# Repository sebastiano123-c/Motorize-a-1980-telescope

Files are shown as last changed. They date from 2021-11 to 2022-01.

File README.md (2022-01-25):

<!-- <div align="center">
<img src="https://static.tvtropes.org/pmwiki/pub/images/HHguide.jpg"  width="120" height="150">
</div>
<div align="center">"Always know where your towel is"  -   Hitchiker's guide to the galaxy </div> -->
<h1 align="center">
  <b>
    Motorize-a-1980-telescope
  </b>
</h1>
<h3  align="center" style="font-style:italic; color: Gray">Kepler1 - a OnStep project</h3>
<p align="center">
   
  
</p>
<!-- 
<h position='center'>
# Motorize-a-1980-telescope
## _Kepler1 - a OnStep project_
</h> -->

# Description
If you, like me, find an old dusty telescope in our garage, wouldn’t you want it to work like one of the best motorized telescopes? Here, you will find the transformation of my equatorial Urania telescope on the way to 2.0.

# Theory
All the steps are reported in the [documentation](https://github.com/sebastiano123-c/Motorize-a-1980-telescope/blob/main/documentation.pdf).
The software parts are provided by [OnStep](https://github.com/hjd1964/OnStep) and there you'll find how to install the software and choose your best approach that fits your mount.
3D printed parts are stored in the [Hardware](https://github.com/sebastiano123-c/Motorize-a-1980-telescope/tree/main/Hardware) folder.
Pinout design for the electronic parts are visible in the [Setup](https://github.com/sebastiano123-c/Motorize-a-1980-telescope/tree/main/Setup) folder.

# Roadmap
In the future, we will try to obtain better tracking resolutions and faster slew rates.

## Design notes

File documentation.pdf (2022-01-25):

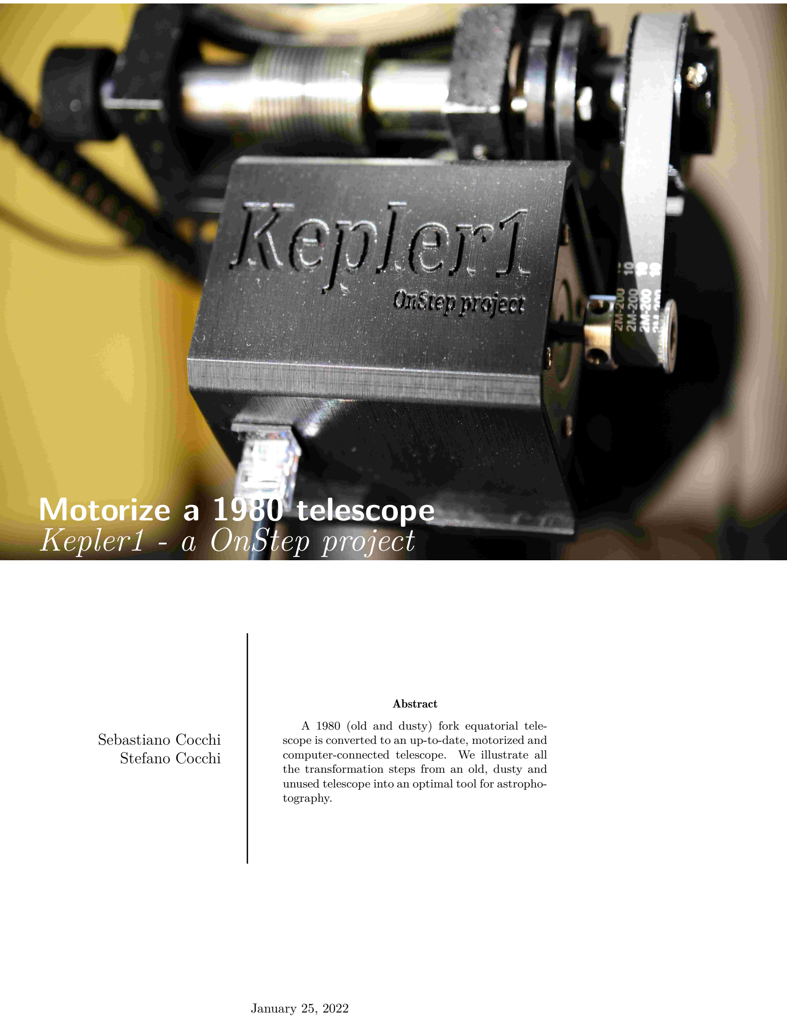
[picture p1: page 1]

# Motorize a 1980 telescope Kepler1 - a OnStep project

Sebastiano Cocchi
Stefano Cocchi

Abstract

A 1980 (old and dusty) fork equatorial telescope is converted to an up-to-date, motorized and computer-connected telescope. We illustrate all the transformation steps from an old, dusty and unused telescope into an optimal tool for astrophotography.

January 25, 2022

## Contents

Introduction | 1
1 Telescope description | 1

1.4 Telescope substitution: from Urania’s tube to

2 Electronics | 2

2.6 Sensors: WiFi connection, Real time clock

3 Mechanization | 6
4 Cable management | 6
5 The software | 8
6 Tests | 9
7 Conclusion | 9
Appendix | 11

## Introduction

The Kepler1 project led to the developing of a telescope mount with right ascension (RA), declination (DEC) and focuser (FOC) movements fully motorized and controlled by the won-
derfull software OnStep with a precision well below 1 | ′′ in both

RA and DEC mechanism starting from a 1980 telescope. The final setup components are reported in section 7, go there to find out our conclusions.
In section 1 we describe the starting telescope mount, the substitution of the old telescope tube with a new one and the installation of the latter.
In section 2 we show the electronics we have used; starting from the ESP32 board WeMos D1 R32 with CNC3 shield we describe the motor drivers, the components for the WiFi connection, the time clock and the weather sensors. We also describe some modifications to the CNC3 shield to improve the microstepping control with gotos.
In section 3 we describe the mechanisms for the RA movement, some versions of the DEC movements and the FOC motorization.
In section 4 we explain how to cleverly attach and detach the motors from the main board using ethernet cables.
In section 5 we explain the basics of the software OnStep and some additional apps that we use for the tracking (i.e. PHD2) and Stellarium.
In section 6 we briefly show the tracking system and some guiding tests operated with the mount with the results.
The result of our work is the telescope in figure 1.

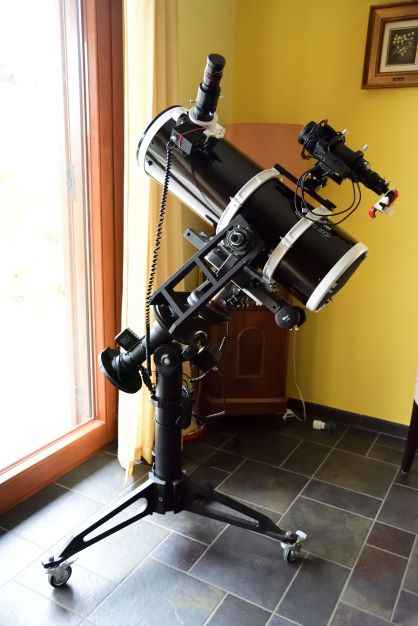
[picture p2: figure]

Figure 1: Final result: our brand-new telescope.

## 1 Telescope description

The starting point of the project is of course the telescope. In our garage, for many years, a 1980 Urania telescope has eaten a lot of dust. The telescope’s mirror resent of years in humidity and temperature jumps in the garage. In the beginning, we have cleaned the mirror with soap and water, but still seemed to be a bit compromised. We do not talk long about this telescope, since we have soon substituted it with a brand-new Skywatcher Quattro. The latter is placed on the Urania mount, since it is still a nice mount and, in our advice, has still not surpassed robustness. Indeed, the mount is a very heavy (telescope and mount totally weight 35kg!) equatorial and motorized (still works!) mount.

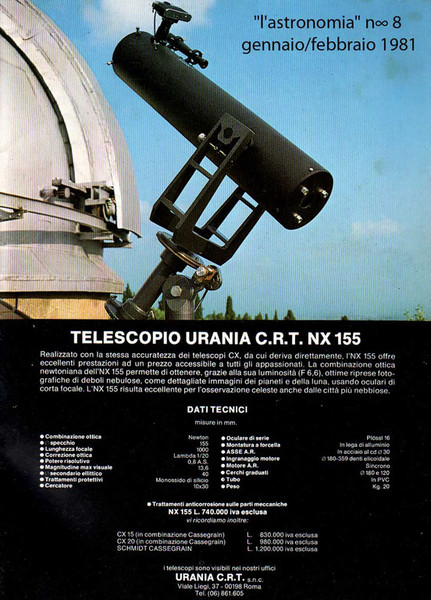
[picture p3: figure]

(a) Urania telescope and mount.

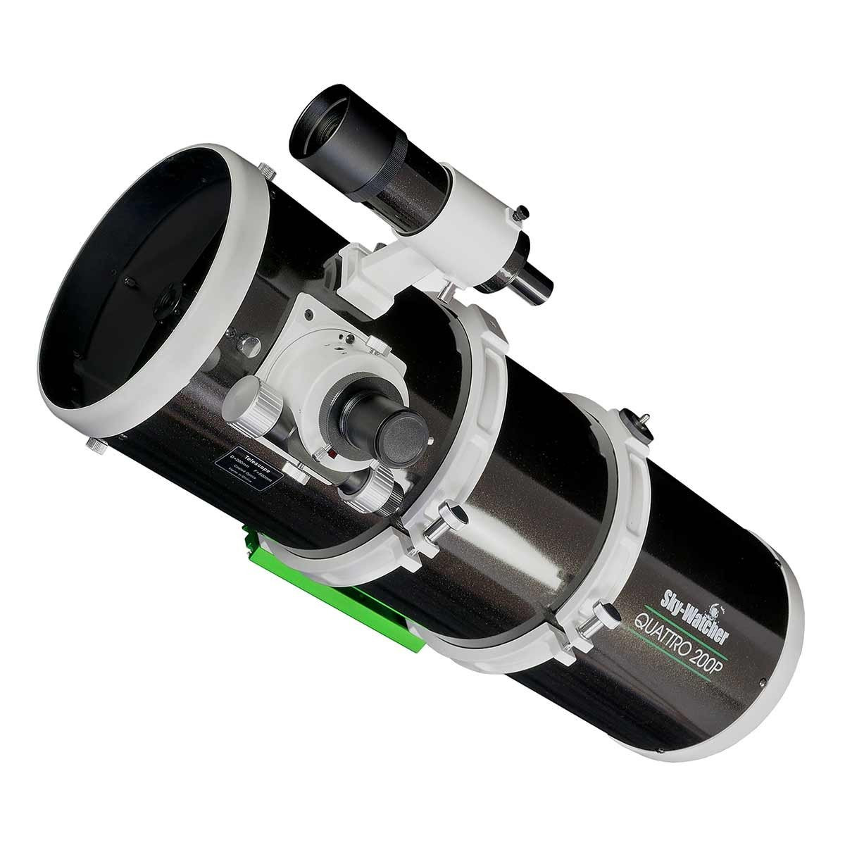
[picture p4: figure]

(b) Skywatcher Quattro telescope.

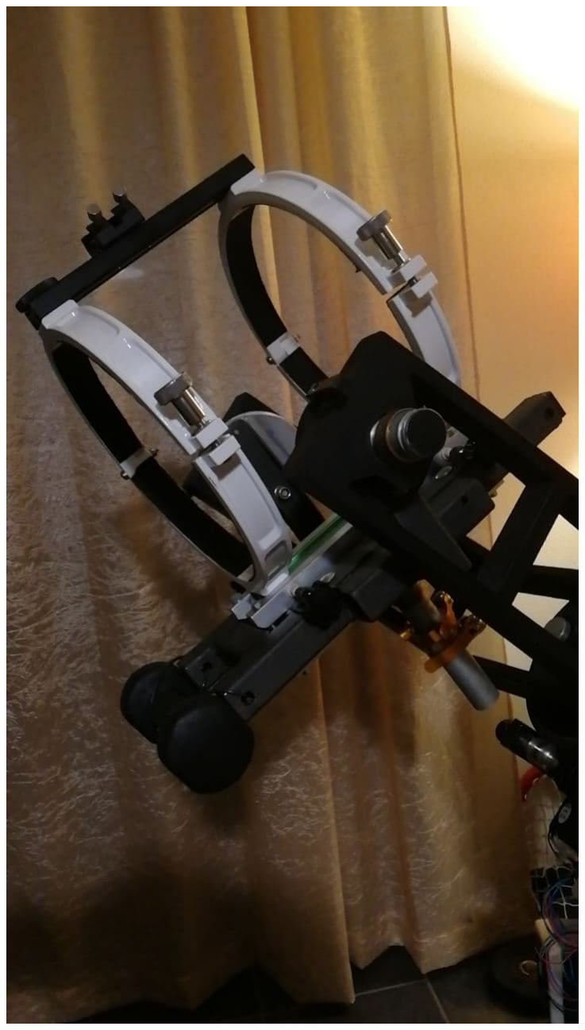
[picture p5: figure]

(c) The mechanism built to insert Skywatcher’s telescope into the Urania robust mount.

Figure 2: The transition between the old telescope to the new telescope: (a) the starting point telescope, (b) the new telescope, (c) and
(d) the telescope seat used for the substitution.

For our money, but most importantly for our fun and entertainment, we decided to modernize our old telescope.

### 1.1 Urania telescope

We briefly add the specifics of the old Urania telescope, as a sort of respect for many years of honorable work before the deep dark in the garage.
The telescope is a Urania C.R.T. NX 155, as the one in figure 2a.
Specific’s name | value
type | reflector
technique | Newton
material | PVC
weight (kg) | 10
aperture (mm) | 155
focal length (mm) | 1000
focal | f/6.5
resolution power | 0.8
limit magnitude value (mag) | 13.6
Mirror Treatment | Silica monoxide

Table 1: Urania C.R.T. NX 155 specifics.

### 1.2 Telescope’s mount

The telescope is place onto an aeronautic Aluminum tripod equatorial mount.

Specific’s name | value
weight (kg) | 25kg
type | fork
material | Aluminum alloy
RA axis diameter (mm) | 30
RA axis material | cadmium steel
RA motor | 3W synchronous

Table 2: Urania’s mount specifics.

Starting from the bottom: three pods of 45cm depart from a central post. Each one has a wheel which permits the structure to move freely and then to fix the position using stops. The central post terminates with the second axis holder whose inclination can be adjusted using a big screw. Using a digital inclinometer we fix the axis to be at 45.75′ with respect to the ground.

This axis must be aligned with the Polar star (labelling the North). In this way, a 220 volt AC 3W synchronous motor can follow the sky movement.

Departing from this second axis, a two-arms fork is free to rotate around two degrees-of-freedom defining the right ascension (RA) and the declination (DEC). The two arms are separated by the distance d = 260mm which is enough to fit the Urania telescope aperture.

### 1.3 Skywatcher 8P Quattro telescope

Skywatcher 8P Quattro Newtonian telescope (figure 2b) offers an optimal astrophotography performance. For this reason we have decided to substitute the Urania telescope with this brand-new Skywatcher telescope.

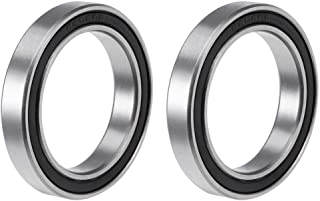
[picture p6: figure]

(a) Internal bearing mounted on one fork arm.

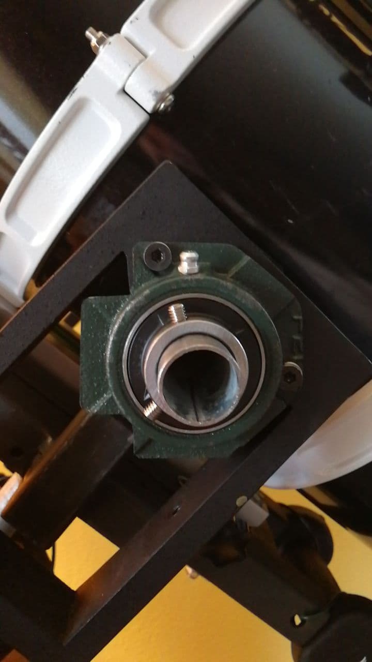
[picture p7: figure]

(b) External bearing mounted on one fork arm.

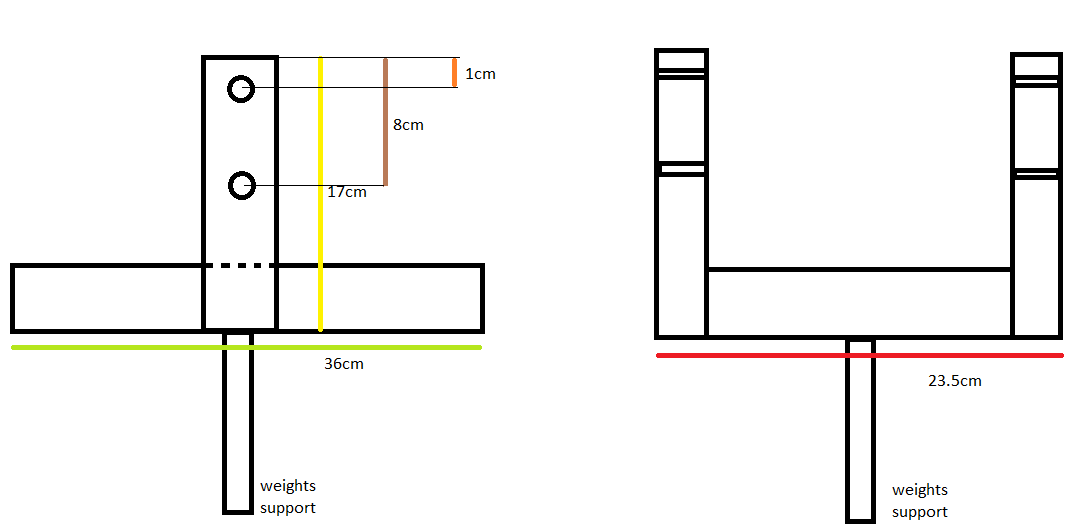
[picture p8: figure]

(c) Schematic view of the telescope mount insertion. This represents only the installation build with some squared metal bars upon which the two white loops (which hold the telescope tube) are fixed and are not illustrated in this scheme. The two holes in each arm serve to fix the structure on the mount.

Figure 3: Telescope seat details.

Specific’s name | value
type | reflector
technique | Newton
material | Carbon
weight (kg) | 8.0
aperture (mm) | 200
focal length (mm) | 800
focal | f/4
resolution power | 0.58
limit magnitude (mag) | 13.3
collect light | 820
magnification | 400
Mirror Treatment | Aluminum Coating
Focuser | Crayford dual-speed 50.8/31.8

Table 3: Skywatcher 8P Quattro
Since the Skywatcher telescope does not fit in the fork, we have thought to build a "saddle" onto which placing the telescope. The specifics of this installation are shown in the following section.

### 1.4 Telescope substitution: from Urania’s tube to

Skywatcher’s tube

Passing from the Urania telescope to Skywatcher telescope we have faced the problem of how to insert the latter in the telescope mount. Indeed, since Skywatcher’s telescope tube outer diameter is 235mm it does not fit nicely inside the mount fork.

Our solution is to insert a seat in which to place the telescope, see figure 2c. The barycenter of the telescope is not centered with the DEC axis, thus we have settled a post capable of holding weights to balance the forces, see figure 3c.

The scheme with distances is visible in figure 3c.

Lastly, to enhance the fluidity of motion and reduce the backlash, the rotation mechanism is enriched with a system of two bearings for each fork arm, one is place inside, see figure 3a, and one is fixed externally on the mount, see figure 3b.

The total weight of the mount with this modification is attested on 40kg.

## 2 Electronics

The circuit design is represented in figure 4c. In this section we expose the electronic components used in the circuit.

### 2.1 ESP32

ESP32 is a series of low-cost, low-power system on a chip microcontroller with integrated Wi-Fi and dual-mode Bluetooth. We’ve bought the ESP32 D1 R32, the one in figure 4a, for better attaching the motor using the CNC shield V3 (which is briefly explained in the following).
We decided to follow the "WeMos R32 and CNC V3" On-Step project (at https://onstep.groups.io/g/main/wiki/19670). (https://onstep.groups.io/g/main/wiki/19670) OnStep is an open source software providing the control of four stepper motors (RA, DEC, focuser and rotator for astrophotography), weather sensor handling, Wi-Fi and Bluetooth connection, polar alignment and other nice features.

### 2.2 CNC Shield V3

To better optimize space and wires connections, we have bought a CNC Shield V3 (a.k.a. CNC3), see figure 4b.
It is a printed circuit board (PCB) built for 3D printers. The shield is attached directly above the ESP32. It has four slots, each one can host a motor driver, thus using this shield there can be handled four stepper motors: RA and DEC motors, first focuser and photography rotator or second focuser. This shield can be "manipulated" to obtain better performances.

### 2.3 Motor drivers

A stepper motors works only with a driver chip that controls the motor movements. Three types of drivers have been used during the configuration of the setup.

1. DRV8825;
2. TMC2209;
3. TMC2208.

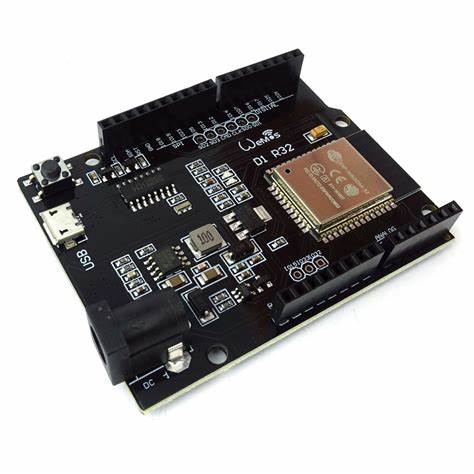
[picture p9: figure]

(a) ESP32 D1 R32 picture.

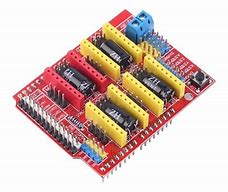
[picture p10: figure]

(b) CNC3 Shield V3.

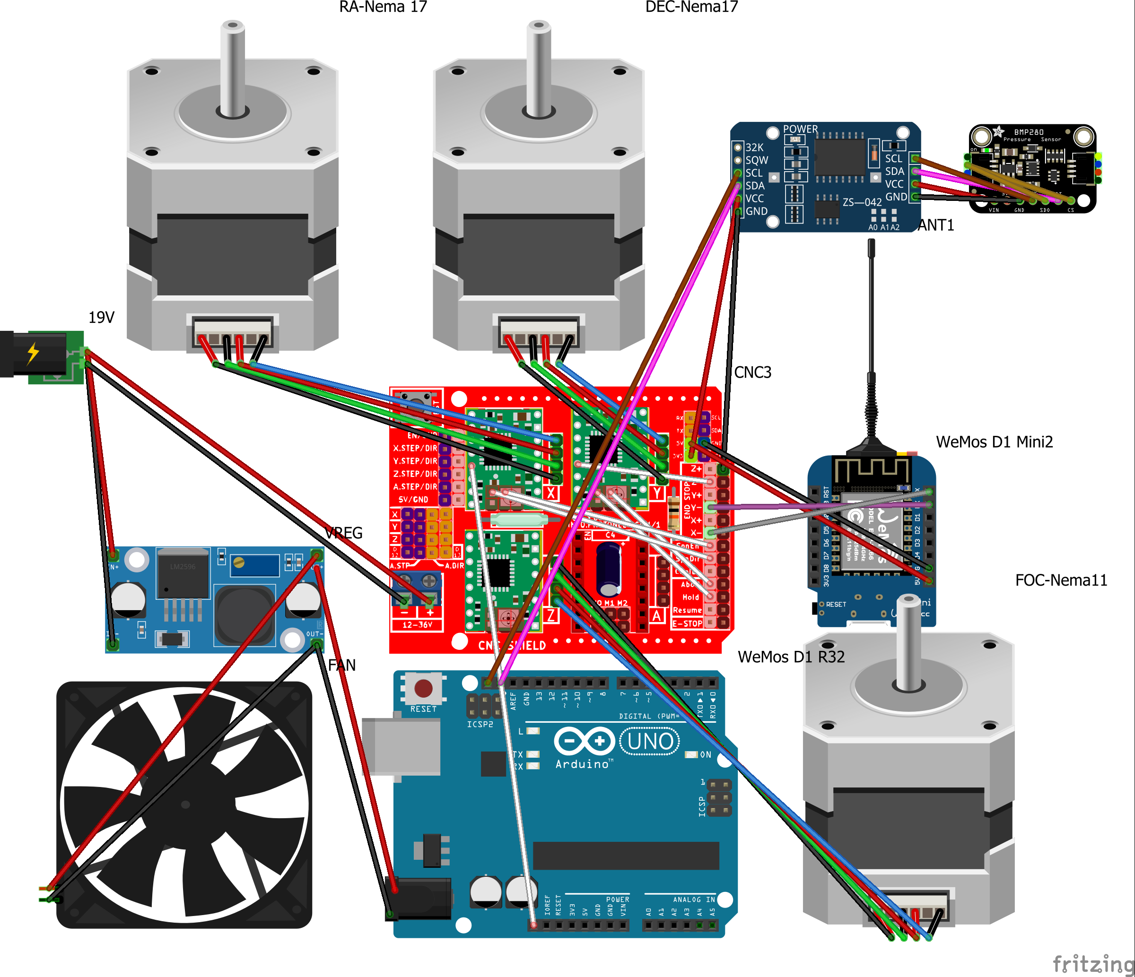
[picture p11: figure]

(c) Circuit design. Here (https://github.com/sebastiano123-c/Motorize-a-1980-telescope/blob/main/Setup/circuit-design_bb.png) can be found the png file. Figure 4: Main board components: (a) WeMos D1 R32 ESP32 board, (b) CNC shield V3 and (c) the circuit design: the Arduino board is instead a ESP32 board, like the one of figure (a); the white cables are our modifications on the board.

In each driver the right amount of current is set, otherwise the stepper motor could work improperly. This current
depends on the stepper motor current per phase parameter. Typically, drivers have a tunable screw for the tension Vref . For each type of driver, the formula to calculate the tension Vref depending on the current/phase are different.¹
The procedure is the following:
- rotate the screw in the counter clock direction;
- using a multimeter, check that the tension is zero;
- slightly rotate the screw until the tension is the desired one.

We recommend reducing the theoretical value by a 10%-30% to prevent motor dangers.

### 2.3.1 DRV8825

For these drivers the tension to be set is roughly the half of the value of the nominal current/phase of the motor. For example, if the motor has a current/phase 1A, the tension would be 0.5V.

Current phaser (A) | Current (A)
0.90 | 0.45
2.00 | 0.90

Table 4: DRV8828 drivers setup current. Note that we have set a value smaller than the one calculated to prevent motor to break.

### 2.3.2 TMC2208 and TMC2209

For these drivers the tension value is roughly the same of the current/phase value, e.g. if I = 1A the tension would be Vref = 1V. Be aware that the TMC2208 has a maximum current output of 1.2A.
The calculation is

I
√
2

=

325mV
110mΩ + 20mΩ

·

1
√
2

·

Vref
2.5V

⇒ Vref = I · 1Ω.

Remember to reduce to value by a 10%-30%.
Driver | Current/phase (A) | Current (A)
TMC2209 | 0.90 | 0.81
TMC2209 | 2.00 | 1.63
TMC2208 (focuser) | 0.67 | 0.50

Table 5: TMC22XX drivers setup current. Note that we have set a value smaller than the one calculated to prevent motor to break.

### 2.4 CNC3 and TMC2209 modifications

CNC3 shield does non permit "on the fly" change of microstepping since microsteps are achieved via the MS0/MS1/MS2 fixed jumpers below the motor drivers. This means that you cannot have different microstepping for tracking and slewing unless you use TMC2130 or TMC5160 through SPI interface. To overcome this CNC3 limit when using other drivers (e.g. TMC2209 that are very silent, guarantee a 2A current per phase and are somehow cheap), it is necessary to do some soldering on the CNC3 and on the TMC2209 and modify the pinmap "Pins.CNC3.h".

1See this (https://all3dp.com/2/vref-calculator-tmc2209-tmc2208-a4988/) for more details.

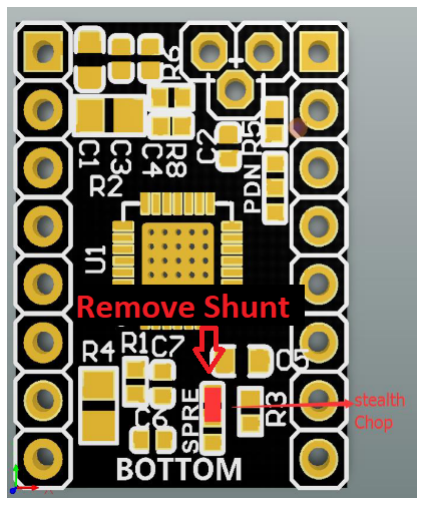
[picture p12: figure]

(a) TMC2209 driver with highlighted modifications.

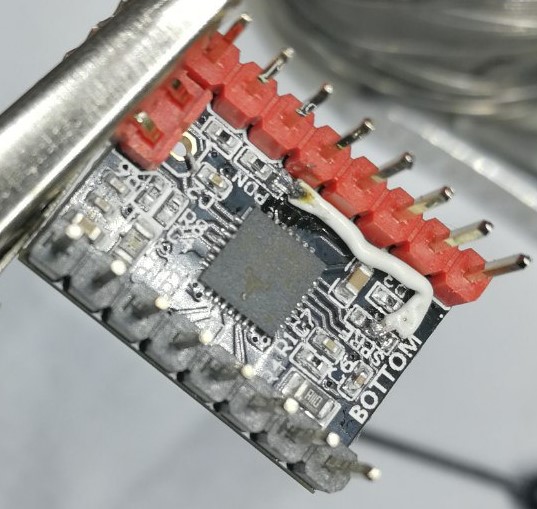
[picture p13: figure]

(b) Connection of the Spread pin to pin 5 by

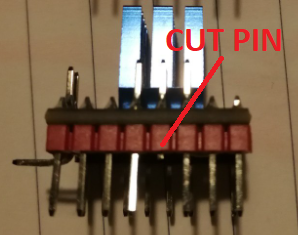
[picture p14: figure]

wire. | (c) Cut low pin 5.

Figure 5: TMC2209 modifications.

### 2.4.1 Microsteps control

First of all it is necessary to configure the TM2209 stepper driver (TMC2209 Bigtreetech v1.2) to remove the Spread shunt (that controls StealthChop vs SpreadCycle mode) on the TMC2209 board and then wire connect the Spread to pin 5 of J1, see figures 5a 5b.
Finally, you have to cut the low pin 5 of J1 on the TMC2209 driver since it is shortcutted with pin 6 (CLK) on the CNC3, see figure 5c.
At this point, we have a wire connected (some soldering) the MS0 and MS1 of Axis X to the SpnEn and SpnDir pins of CNC3 respectively. In the same way, we have a wire that connected the MS0 and MS1 of Axis Y to the HOLD and ABORT pins respectively. In this way, we are able, after modifying the pinmap in "Pins.CNC3.h" to control the microstepping in Tracking and Goto both in RA and DEC. You can find the modified Pinmap "Pins.CNC3.h" here. (https://github.com/sebastiano123-c/Motorize-a-1980-telescope/blob/main/OnStep/src/pinmaps/Pins.CNC3.h)
The last modification is simply to connect with a wire jumper pin 5 of TMC2209 of AXIS X to the pin IO0 of the We-Mos D1 R32 as well as connect pin 5 of TMC2209 of AXIS Y to the pin Z− of the CNC3. With this done we able to set programmatically (via Config.h) the SpreadCycle (StealthChop) mode using the TMC2209_QUIET (TMC2209_VQUIET) constants.
Here (https://github.com/sebastiano123-c/Motorize-a-1980-telescope/blob/main/OnStep/Config.h) is the updated "Config.h".

### 2.5 Power supply

The power supply is provided by a 19V 5A power supply as in table 6.
voltage output (V) | current output (A)
19.3 | 4.74

Table 6: Nominal tension and current outputs of the
power supply.
For our initial purposes it was enough, indeed 5A are enough to feed quite well two stepper motors and a poor electronics. A rough estimation poses 1.8A for RA motor, 0.9A for DEC motor and few milliampéres for the ESP32. The reader is strongly encouraged to check the total current its circuit needs before buying a power supply.
To provide the 3.3V tension to the microcontroller, a IC-QUANZX voltage regulator is place between the power supply and the ESP32.

### 2.6 Sensors: WiFi connection, Real time clock

(RTC) and weather sensor (BMP280)

OnStep contains the so-called Smart Web Server (SWS) that provides WiFi (or Ethernet) connections using an IP but it does not exploit the native ESP32 chip for the WiFi connection; To command the mount via WiFi a ESP8266-12F WeMos D1 mini must be connected to the CNC3.² Many devices support this type of connection including cell-phones, tablets, laptop/desktop computers, etc. Using this library, it is possible to use programs such as Stellarium via ASCOM drivers provided by the OnStep project. (http://www.stellarjourney.com/index.php?r=site/software_telescope) We have added an external antenna to enhance the WiFi connection range.³ The weather sensor BMP280 is modified as follows: the CSB and the SDO pins are connected directly to the Vcc. The sensor is then attached directly to the RTC module Ds3231. The RTC, BMP280, the WiFi module and the stepper motors are connected to the WeMos ESP32 D1 R32+CNC3 board as in figure 4c.

## 3 Mechanization

The motorization of the telescope passes through two mechanics adjustments:

1. motorize the RA movement, exploiting the native tracker mechanism;
2. motorize the DEC movement, which natively has no gears.

Before entering in the details, we define the stepper motors used in the setup.

2For the pinout maps look at this connection diagram. (https://onstep.groups.io/g/main/wiki/19670) 3Take a look at this (https://www.instructables.com/External-Antenna-for-ESP8266/) to see how to do that.

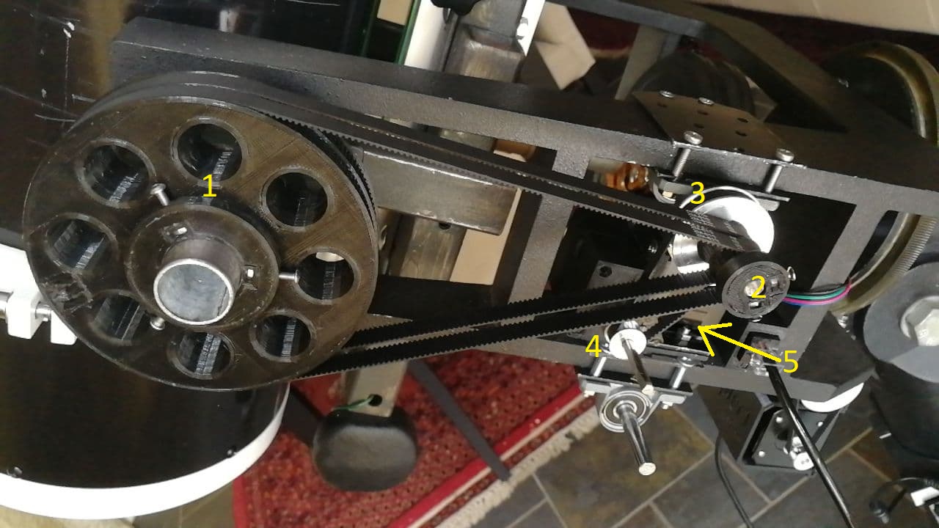
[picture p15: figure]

(a) DEC V1 mechanism.

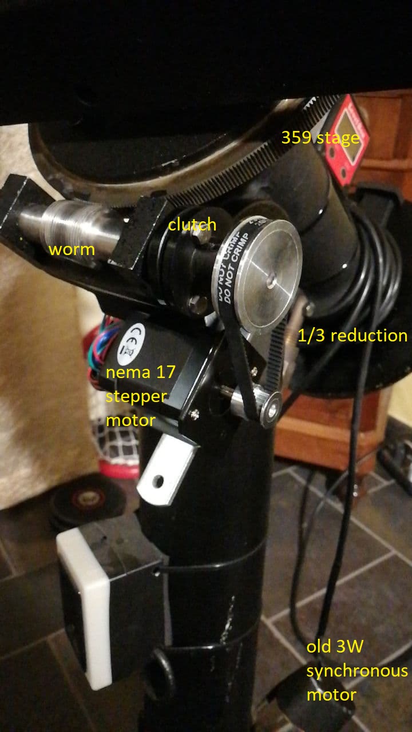
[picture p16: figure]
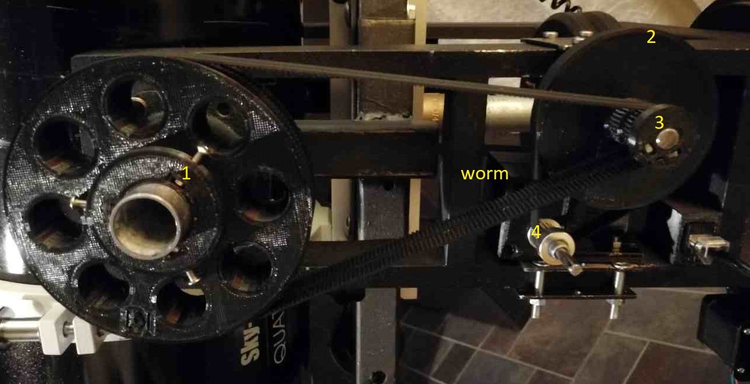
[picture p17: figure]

(a) DEC V1+ mechanism. | (b) RA mechanism.

Figure 6: RA and two of the many versions of the DEC mechanization.

### 3.1 Stepper motors

In this subsection we write the specifics of the stepper motors used for the RA and DEC mechanization (for both we have used nema 17 motors) and the focuser (developed with a nema 11 stepper motor).

### 3.2 RA motorization

The telescope’s mount has already a tracking mechanism motorized by a 220volt AC 3W synchronous motor. So, in principle, it is only a matter of substitute this old motor, with a new programmable stepper motor.
The gears are composed by:
- a 359 teeth stage (1 tooth for each degree, fantastic);
- an endless screw (worm) mounted on a shaft through a clutch.

Using this structure, for a continuous sky tracking, the elder motor would complete a round of the worm in 4 minutes. Thus, this mechanism rotates the mount with the velocity of a degree in 4 minutes (which is the velocity of the sky moving away in the night).
We have reduced the ratio by a third adding two other pulleys (see figure 6b): 60 teeth pulley positioned in the shaft and a 20 teeth pulley on the motor shaft.
ratio gear 1 | ratio gear 2 | total ratio
1/360 | 1/3 | 1/1080

Table 7: Total reduction of RA mechanization.
We have chosen to install a nema 17 stepper motor with the specifics in table 15

### 3.3 DEC motorization

The mechanization of the DEC axis was a bit more complicated since there was not a built-in gear to use. We tried different versions. A first successfully try was to exploit a stand-alone disk. On the edge of the latter are present some ticks and grades: it was used a declination angle teller.
As told above, we have tried different configurations, but same stepper motor is used.

### 3.3.1 DEC V1

Using a 3D printer we have designed a double-belt pulley. Then, a 1/10 ratio is obtained using a worm gear and another 1/3 is obtained between the worm and the final gear. The total reduction with all gear specifics is reported in table
8. Figure 6a is a picture of the mechanism. The precision of the mechanism is

δth. = 0.28′′, δest. = 0.96′′

where th. stands for theoretical and est. stands for estimated.

DEC-V1 stages
Gear number | 1 | 2 | 3 | 4 | worm
number of teeth | 180 | 30 | 60 | 20 | 10
total ratio | ∼
| 1
| 180

Table 8: DEC mechanism’s gear specifics.

### 3.3.2 DEC V1+

Starting from the DEC V1, we have designed a new gear to get a bigger reduction ratio (this is the reason for the +). The total reduction with all gear specifics is reported in table 9. Figure 6a is a picture of the mechanism. The precision of the

mechanism is

δth. = 0.14′′, δest. = 0.48′′

where th. stands for theoretical and est. stands for estimated.

DEC-V1+ stages
Gear number | 1 | 2 | 3 | 4 | worm
number of teeth | 180 | 30 | 120 | 20 | 10
total ratio | ∼
| 1
| 360

Table 9: DEC mechanism’s gear specifics.

### 3.4 Focuser motorization

Another improvement is the motorization of the dual speed Crayford focuser. Using a nema 11 stepper motor, we have created the motor supports and the gears using a 3D printer. The reduction stage is 1/3, and the mechanism is visible in figure 7c.

## 4 Cable management

The wiring between the electronics and the motors is made focusing on the main idea to attach and detach them rapidly. We thought to use Ethernet cables. They are a versatile solution but how to connect them to the four cables governing the stepper motor?
Stepper motors have four cables, see figure 8, which have to be driven to the CNC3.

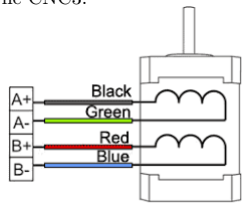
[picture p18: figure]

Figure 8: Stepper motor cables scheme.

### 4.1 Ethernet cables

Ethernet cables are composed typically by 8 thin cables, each one carrying low current, approximately 0.3 − 0.5A. Since stepper motors require currents of the order of 1A, we decided to use them in couple, according to the general Ethernet cabling scheme. Thus, the four motor cables are doubled and fixed into the eight way Ethernet socket.
Then, the main box is prepared to receive the Ethernet cables. In the most remote drawers of the garage, we have found an old and burned electronic card with four Ethernet sockets, a power supply entry and an on/off switch. Using a multimeter we have checked the pins of each slot and created the connections to the CNC3 shield.
In figures 7a, 7b and 7c are shown some examples of Ethernet wiring.

### 4.2 Plastic boxes

Using a 3D printer, we have created the focuser motor bracket with the Ethernet exit, and so we did for the RA motor. The microcontroller, the CNC3 shield, the power supply and all the electronics have been thrown in a box. The stepper motors drivers do not get hot, nevertheless we have decided to put a 12V fan in the box. In figures 7a, 7b and 7c are shown the resulting plastic boxes.

## 5 The software

Now comes the software part. In our mind, we wouldn’t want to spend much time on programming. We desired a plug-andplay solution, or something similar. A software with easily controlling and possibly which can talk via ASCOM drivers with Stellarium (or others), PHD2 and others astrophotography programs.

### 5.1 OnStep

On the internet, we have found a great, open-source, free and customizable software called OnStep.⁴ We have followed the instructions for the WeMos D1 + CNC V3 project, configured the Config.h file and upload the sketch on the ESP32 board. Finally, the box is placed on the mount and connected with the Ethernet cables to the motors. OnStep is actually a wonderfull project. Don’t miss it, and stay tuned on it!

### 5.2 PHD2

Push It Dummy-2 (PHD2) is the software that controller the auto-guiding system. PHD2 is telescope guiding software that simplifies the process of tracking a guide star, letting you concentrate on other aspects of deep-sky imaging. There are plenty tutorials on the internet showing how to use PHD2, so we do not enter so much into details.⁵ But we only want to stress out that, after few important configuration passes, the auto-guiding is really simple and promises very good results!

### 5.2.1 Wizard configuration

Connection is really simple using the "wizard" option suggested in every tutorials. The "unbinned pixel size" is one of the first parameters you have to fix in the wizard which are not quite clear. You should be able to get the unbinned pixel size from the camera spec sheet or the manufacturer’s web site. If this is not the case, you can get the unbinned pixel size by taking the dimension of the sensor and diving it by the number of pixels.
The "bin level" is the technique to combine proximal bins to form a "superpixel".⁶ This has the effect of reducing the noise but at the price of reducing the image definition. Another remarkable option to fill is the telescope mount’s driver, which in this case are the ASCOM OnStep telescope drivers.

4Wiki groups:https://onstep.groups.io/g/main/wiki/3860.
Github:https://github.com/hjd1964/OnStep.
5https://www.youtube.com/watch?v=Kd4qzW7uV38 or the pdf https://openphdguiding.org/man-dev/Basic_use.htm.6https://www.photometrics.com/learn/imaging-topics/binning-2.

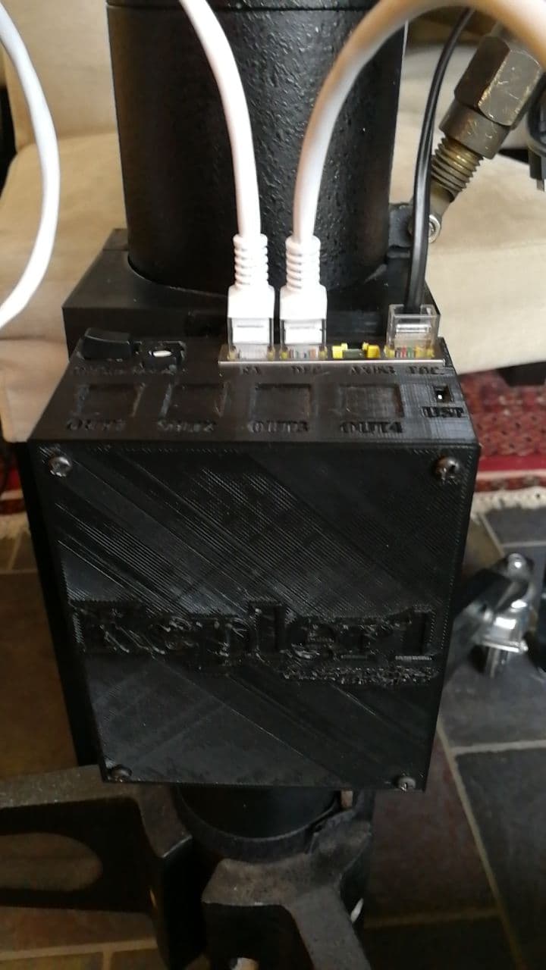
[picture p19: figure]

(a) The main box containing the electronics and its easy management Ethernet connections.

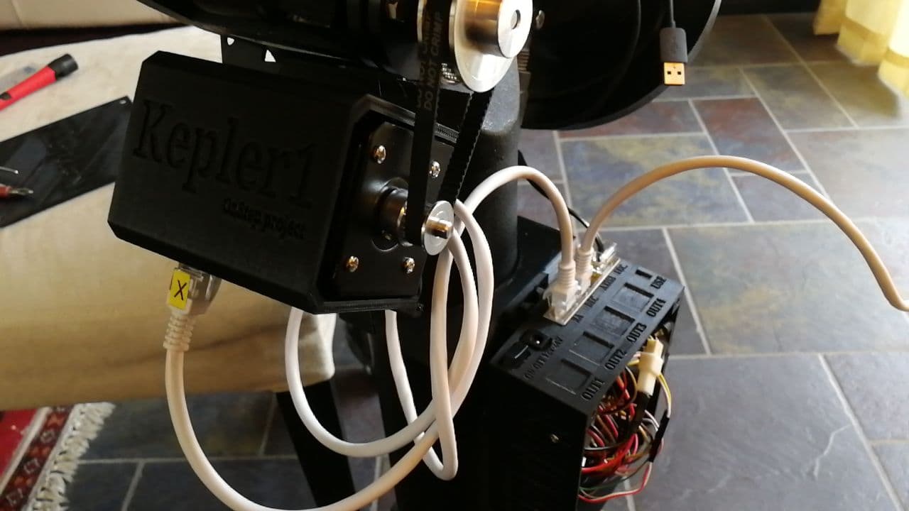
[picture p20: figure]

(b) The RA motor box containing the stepper motor and its Ethernet socket.

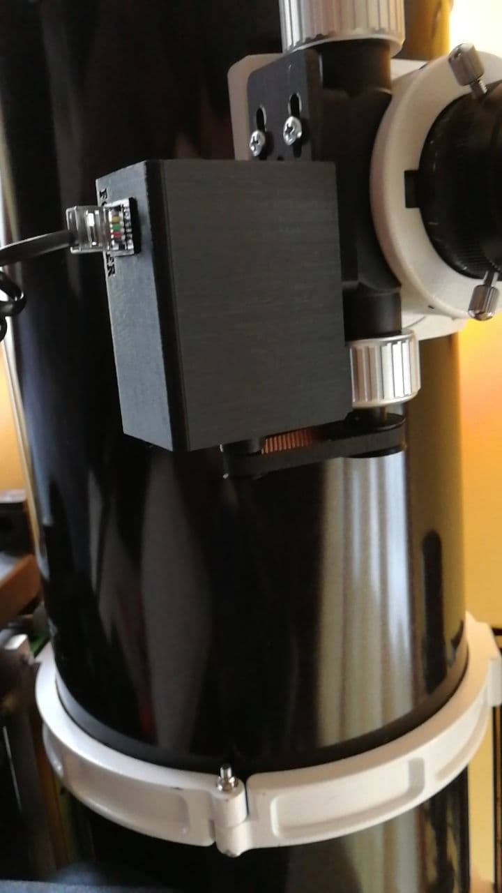
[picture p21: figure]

(c) The focuser box containing the focuser stepper motor and its Ethernet socket.

Figure 7: Plastic boxes.

### 5.2.2 Dark libraries

Before starting the first guiding session, it is useful to spend 5 minutes to create a dark library. To do so, just press the "Dark" tool on the top and create a new dark library. Cover the guidescope, and start the acquisition.
After the acquisition, remove the cover; this should make clearer acquisitions.

### 5.2.3 Connect all!

After the configuration, press the first icon in the bottom left and press "connect all". Now the camera and the mount are connected to PHD2.

### 5.2.4 Calibration

Search a bright star whose declination is between 10 to -10 degrees. Start the acquisition pressing the "cycle" icon (the second from the left), then press the "star with a magnifying glass" that selects the most bright star. Finally, push the PHD2 icon; this will start the calibration and requires few minutes.

### 5.2.5 Guiding

If dark libraries and calibration are done, the guiding can start. If it is not present, search in the settings the plot visualization that let you know the adjustments that PHD2 is doing. In our case, it is a useful tool to see if our work were precisely enough.
A useful tool is the "use multiple stars" in the guiding settings. The latter permits holding multiple star, and we think this is another improvement to stability in auto-guiding.

### 5.3 Stellarium

Stellarium is the software we use to search objects. The impressive feature is that, after paring it via ASCOM drivers with the mount, it is possible to tell the telescope to move at the star pointed out in Stellarium.⁷
The telescope is now free to start few tests to check the goodness of our work!

## 6 Tests

The test are aimed to estimate the precision of the mount. Of particular interest are the test using PHD2 which measure the precision in micro-adjustments for the auto-guiding system. The application used to study the PHD2 plots is the PHD2LogViewer app. The latter can upload all the guiding session you make, since every session is stored in the PHD2 folder. The app also make raw statistical analysis which are good parameters to think about. The root-meansquare (RMS) describe the spread of the data points around some average peak value (like standard deviation). The value of RMS should be 1 arcsecond or lower for a good guiding. Before describing the tests, let us show the tracking system, which is composed of a guidescope and a tracking camera.

### 6.1 Telescope guidescope

On the telescope is fixed a 240mm focal length guidescope Svbony SV106.

### 6.2 Guidescope camera

The camera is an old red SJ1000 action-cam inserted into the guidescope using an adapter.⁸ The result is pretty weird, but it works! Just look at the following sections PHD2 logs!

7See https://www.youtube.com/watch?v=DUdYv311HFw.
8See this useful tutorial https://telescopeguides.com/how-to-use-a-webcam-with-a-telescope/.

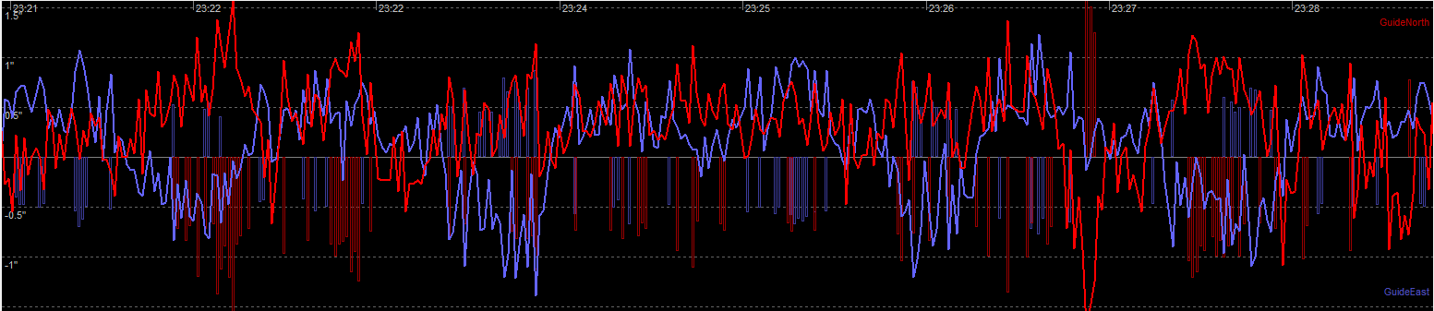
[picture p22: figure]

Figure 9: DEC V1 test: PHD2 log view using arcseconds as units. In pixel the scale is in the range [−0.4,0.4]. The sky seeing was 0.98′′

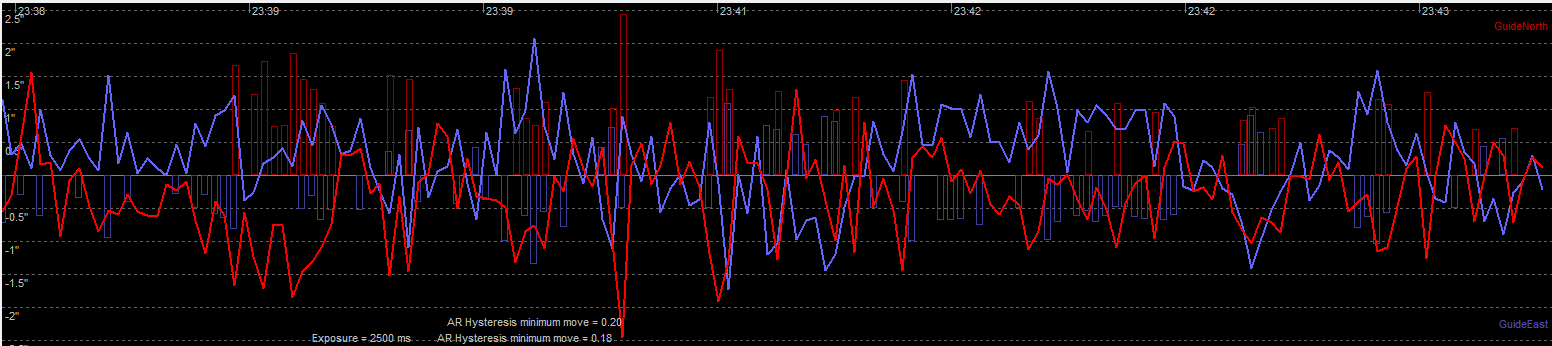
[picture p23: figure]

Figure 10: DEC V1+ test: PHD2 log view using arcseconds as units. In pixel the scale is in the range [−0.5,0.75]. The sky seeing was 1.80′′

### 6.3 DEC V1 test

The DEC V1 has been developed to reduce the mechanism backlash using the idea the less the number of belts gets, the better the guiding is. The resolution power of the mount is reported in table 10. The extrapolated statistics is reported in table 11.

Mechanism | microsteps (x360◦
) | estimated resolution (”)
RA | 19200 | 0.21
DEC | 12800 | 0.65

Table 10: Resolution power using the DEC V1 mechanism. Microsteps is intended as the total number of microsteps around the entire circumference.
After the calibration, we have pointed the Rosetta nebula and start tracking. The result can be seen in figure 9. The sky condition was very nice that night with a seeing of 0.98′′
Statistics | RMS | Peak
RA | 0.47" (0.15 px) | 1.87" ( 0.58 px)
DEC | 0.90" (0.28 px) | -8.12" (-2.52 px)
Total | 1.02" (0.32 px)
Drift | ("/min) | (px/min)
RA | +3.01"/min | +0.94 px/min
Dec | +2.14"/min | +0.66 px/min
Polar Alignment Error | 8.7’

Table 11: DEC V1 test: statistics of the guiding of figure 9.

### 6.4 DEC V1+ test

We have updated the DEC V1 mechanism to DEC V1+ to introduce a more gear reduction and the possibility to decouple the telescope movement from the gear to perfectly balance it. The resolution power of the mount is reported in table 12. The extrapolated statistics is reported in table 13.
Mechanism | microsteps (x360◦
) | estimated resolution (”)
RA | 51058 | 0.24
DEC | 25600 | 0.48

Table 12: Resolution power using the DEC V1+ mechanism. Microsteps is intended as the total number of microsteps around the entire circumference.
After the calibration, we have pointed Aldebaran and start tracking. The result can be seen in figure ??. We point out that the sky condition was not optimal since the seeing was 1.80′′. The latter parameter effect with spurious drifts the guiding.
Statistics | RMS | Peak
RA | 0.66" (0.20 px) | -2.04" (-0.63 px)
DEC | 0.63" (0.20 px) | -2.40" (-0.75 px)
Total | 0.91" (0.28 px)
Drift | ("/min) | (px/min)
RA | +3.39"/min | +1.05 px/min
Dec | -3.65"/min | -1.13 px/min
Polar Alignment Error | 14.5’

Table 13: DEC V1+ test: statistics of the guiding.

## 7 Conclusion

After lots of hours testing our telescope, we can declare what is the best configuration found using the WeMos D1 + CNC3 shield.

Part | component
Microcontroller | WeMos D1 R32 (ESP32) (https://www.amazon.it/ARCELI-sviluppo-dual-mode-Bluetooth-Arduino/dp/B07MBZMYCX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)
Pinmap | CNC3 (https://www.amazon.it/AZDelivery-CNC-Shield-V3-Development/dp/B07YWQJCNY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)
Voltage regulator | 5V (https://www.amazon.it/ICQUANZX-regolatore-Step-Down-Convertitore-Tensione/dp/B07VQ89RZG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)
Time | RTC DS3231 (https://www.amazon.it/ARCELI-DS3231-AT24C32-Precision-Arduino/dp/B07CQW5RMQ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)
Weather sensor | BMP280 (https://www.amazon.it/ARCELI-GY-BMP280-3-3-pressione-atmosferica-precisione/dp/B09DYFNC8G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)
WiFi | ESP8266-12F WeMos D1 mini (https://www.amazon.it/ESP8266-ESP-12F-sviluppo-NodeMCU-Compatibile/dp/B093G72SHN)
RA stepper motor | 17HM19-2004S1 (2.0A) (https://www.amazon.it/STEPPERONLINE-17-motore-passo-passo-Lunghezza-Printer/dp/B00W9A2L3S?adgrpid=117649322299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)
RA motor driver | TMC2209 BigTreeTech v1.2 (https://www.amazon.it/KINGPRINT-TMC2209-Stepper-Driver-Printer/dp/B07WC71M4R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)
RA cable | microphone 8 poles cables (https://www.amazon.it/gp/product/B08PTYKXF3/ref=ppx_yo_dt_b_asin_title_o00_s00?ie=UTF8&psc=1)
DEC stepper motor | 17HM15-0904S (0.9A) (https://www.amazon.it/STEPPERONLINE-passo-passo-Bipolar-42x40mm-stampante/dp/B00W98OYE4)
DEC motor driver | TMC2209 BigTreeTech v1.2 (https://www.amazon.it/KINGPRINT-TMC2209-Stepper-Driver-Printer/dp/B07WC71M4R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)
DEC cable | microphone 8 poles cables (https://www.amazon.it/gp/product/B08PTYKXF3/ref=ppx_yo_dt_b_asin_title_o00_s00?ie=UTF8&psc=1)
FOC stepper motor | 11HS12-0674S (https://www.amazon.it/STEPPERONLINE-passo-passo-Bipolar-28x28x31mm-stampante/dp/B07HHZQMDW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)
FOC motor driver | TMC2208 BigTreeTech v3.0 (https://www.amazon.it/PoPprint-TMC2208-V2-1-passo-passo-silenzioso/dp/B07PFDKSZ9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)
FOC cable | 8 poles cable (https://www.amazon.it/gp/product/B08JQG2CPT/ref=ppx_yo_dt_b_asin_title_o01_s00?ie=UTF8&psc=1)

Table 14: Final setup parts and components.
In table 14 we report the components used for the last test, which is the best result we obtained in terms of guiding and in terms of resolution in table 12. We also show our impressions on the various components tested.

The best drivers are the TMC2209. They are the most silent, the most quick and precise. They are used in our setup for the RA and DEC motors. Otherwise, for the focuser the TMC2208 driver has been used.

The best stepper motor is the 17HM19-2004S1 for its superior precision and power, and we have used it in the RA mechanization because of its robustness at high speeds. It is worth noticing that the most used one in others project is the 17HM15-0904S stepper motor. We have tested it both in the DEC and the RA mechanization, and it does its own work; we have used it in the DEC mechanization because in this mechanism we do not require a lot of torque as in the RA mechanism.

Onstep software has always lived up to expectations. Its existence has allowed us to focus on hardware development and not worry about the software side. In addition, the On-Step ASCOM drivers were very useful to connect the mount to the computer, and we found no problems in the installation, as we explained earlier.

We use the mobile phone’s Onstep app to perform polar alignment. However, at this juncture we find some bugs. Sometimes it happens to set the alignment to four stars, then exit from the section "start align" (for example to focus the eyepiece), and returning to the section of the polar alignment we find that this is set on a single star. This is a problem because pressing "start align" again asks if the mount is "at home", so you have to start again.

As seen in the test section 6, the result are encouraging. The auto-guide seem to be stable and quite good since the RMS is lower than 1 for RA and DEC. Photography with this configuration have been set up with more than 2 minutes per pose (which was impossible for us before the devolving of this project). We think it is possible to increase the exposure time without problems.

As a final consideration, before buying an expensive telescope and mount, consider the idea of converting, if you have it, your old telescope, and then enjoy its developing!

## Appendix

Stepper motors specifics

17HM15-0904S stepper motor
Electronics
Manufacturer code | 17HM15-0904S
Engine type | bipolar
Pitch angle (deg) | 0.9
Torque (Ncm) | 36
Rated current/phase (A) | 0.9
Phase resistance (Ohm) | 60
Voltage (V) | 5.4
Inductance (mH) | 12 ± 20% (1 kHz)

Physical specifications
Frame dimensions (mm²
) | 42x42
Body length (mm) | 40
Shaft diameter (mm) | 5
Stem length (mm) | 22
D-cut length (mm) | 15
Number of cables | 4
Lead number (mm) | 300
Weight (g) | 280

Table 15: Nema 17 (0.9A) stepper motor specifics.

17HM19-2004S1 stepper motor
Electronics
Manufacturer code | 17HM19-2004S1
Engine type | bipolar
Pitch angle (deg) | 0.9
Torque (Ncm) | 46
Rated current (A) | 2
Phase resistance (Ohm) | 1.4
Voltage (V) | 2.8
Inductance (mH) | 4

Physical specifications
Frame dimensions (mm²
) | 42x42
Body length (mm) | 48
Shaft diameter (mm) | 5
Stem length (mm) | 24
D-cut length (mm) | 24
Number of cables | 4
Lead number (mm) | 500
Weight (g) | 370

Table 16: Nema 17 (2A) stepper motor specifics.

11HS12-0674S stepper motor
Electronics
Manufacturer code | 11HS12-0674S
Engine type | bipolar
Pitch angle (deg) | 1.8
Torque (Ncm) | 7
Rated current (A) | 0.67
Phase resistance (Ohm) | 5.6
Voltage (V) | 3.8
Inductance (mH) | 4.2

Physical specifications
Frame dimensions (mm²
) | 28x28
Body length (mm) | 31.5
Shaft diameter (mm) | 5
Stem length (mm) | 20
Number of cables | 4
Lead number (mm) | 300
Weight (g) | 110

Table 17: Nema 11 stepper motor for the focuser motion specifics.

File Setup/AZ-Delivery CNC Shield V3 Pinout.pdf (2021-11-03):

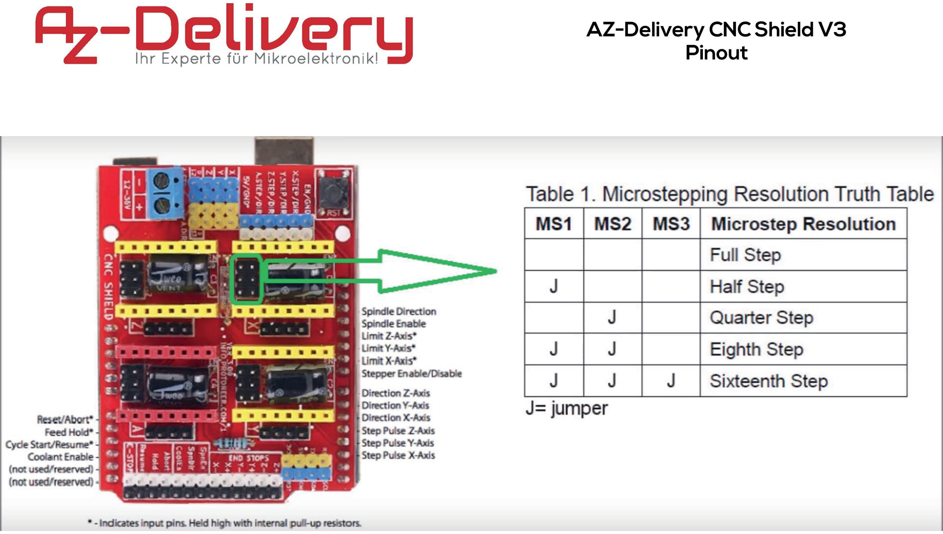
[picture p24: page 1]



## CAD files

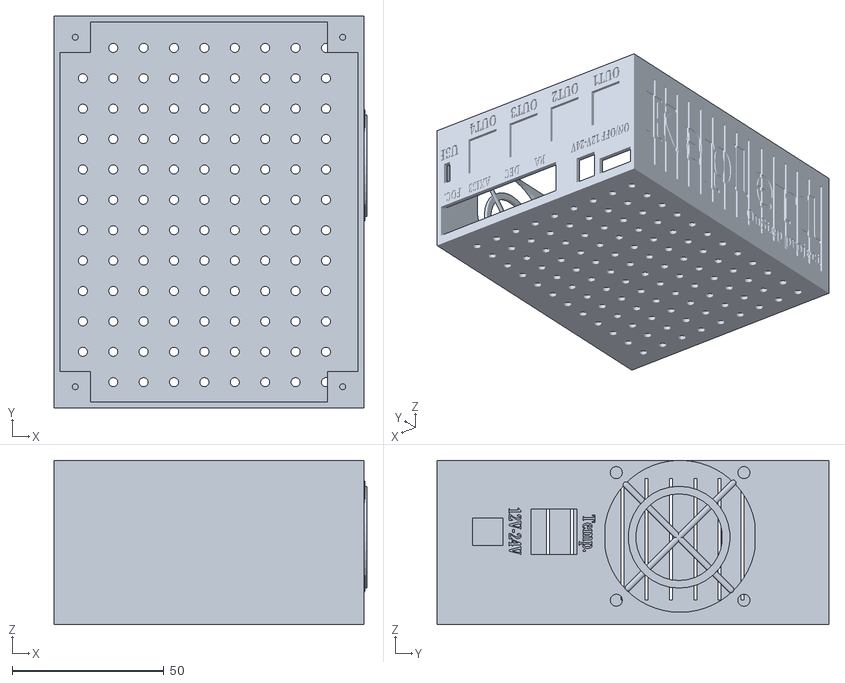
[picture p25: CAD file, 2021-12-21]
Hardware/BOX/BOX-V3.stl
103.0 x 129.0 x 54.0

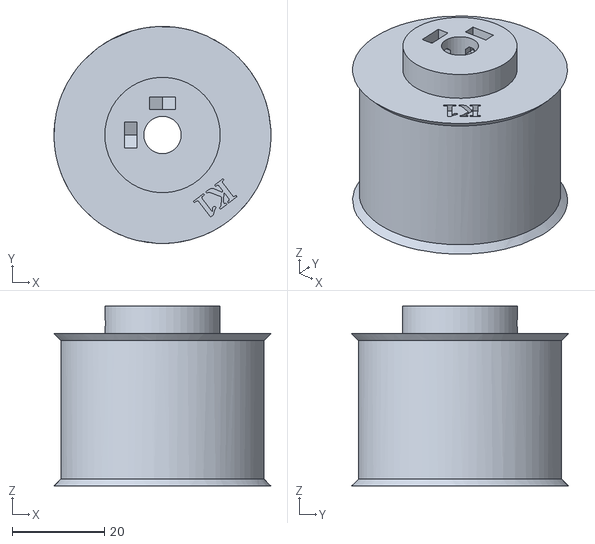
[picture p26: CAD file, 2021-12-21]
Hardware/DEC-mechanism/DEC-Puleggia/GT2-70t_liscia_30mm_foro8.stl
47.0 x 47.0 x 39.0

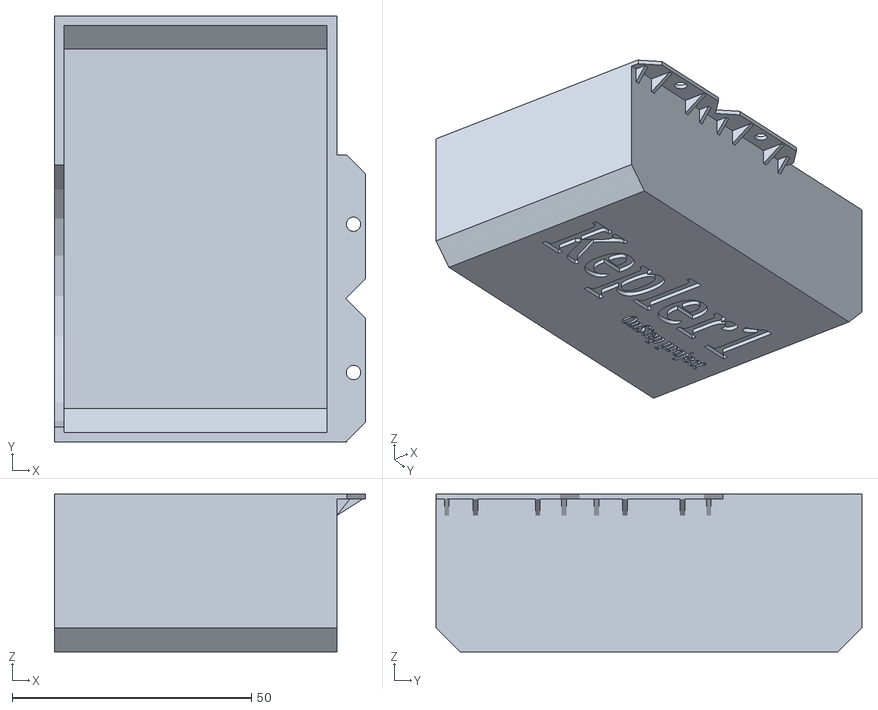
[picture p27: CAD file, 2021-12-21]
Hardware/DEC-mechanism/DEC-V3+-box.stl
65.0 x 89.0 x 33.0

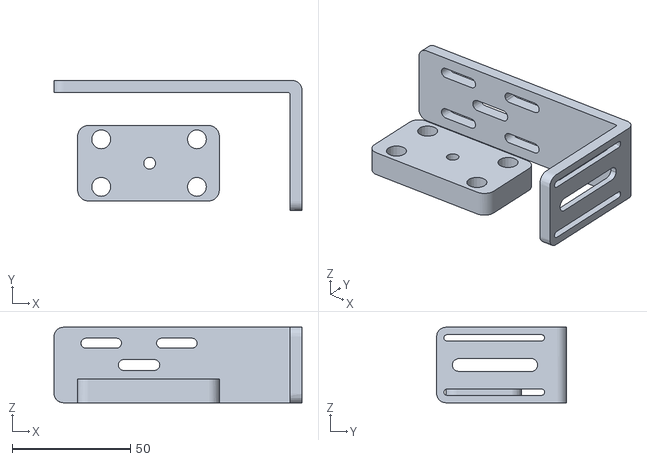
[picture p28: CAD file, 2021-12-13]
Hardware/FOCUSER-mechanism/FOC-motor/FOCUSER-V1.stl
105.0 x 55.0 x 32.0

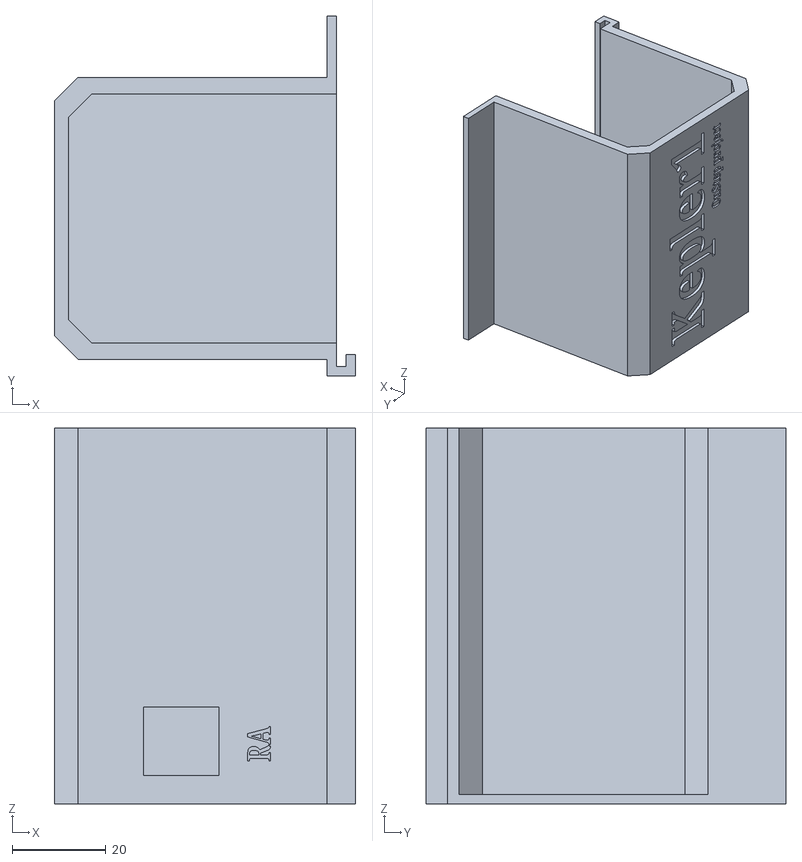
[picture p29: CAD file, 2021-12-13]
Hardware/RA-mechanism/RA-motor-box/RA-MOTOR-BOX.stl
64.1 x 76.5 x 80.0

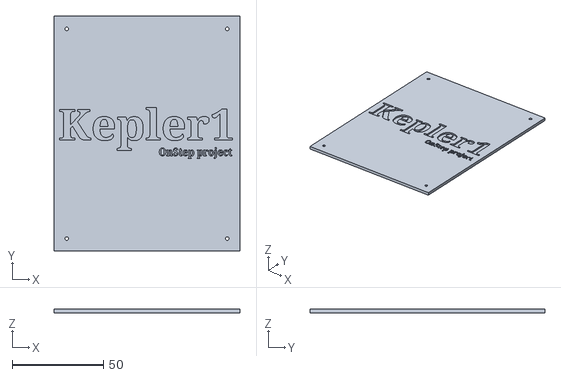
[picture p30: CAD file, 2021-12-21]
Hardware/BOX/BOX-V3-TOP.stl
102.0 x 128.7 x 2.00

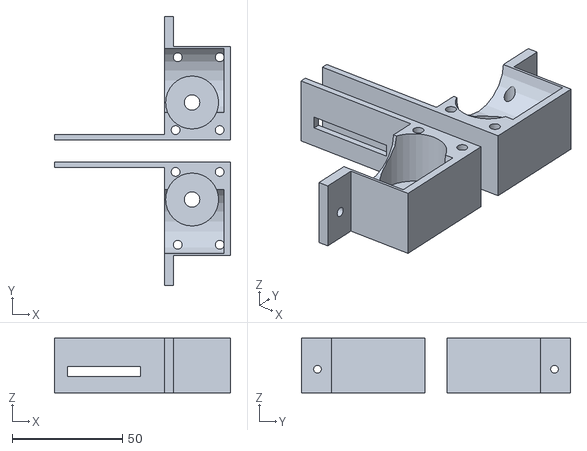
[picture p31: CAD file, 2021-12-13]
Hardware/DEC-mechanism/DEC-Puleggia/WormBox.stl
80.0 x 122.0 x 24.9

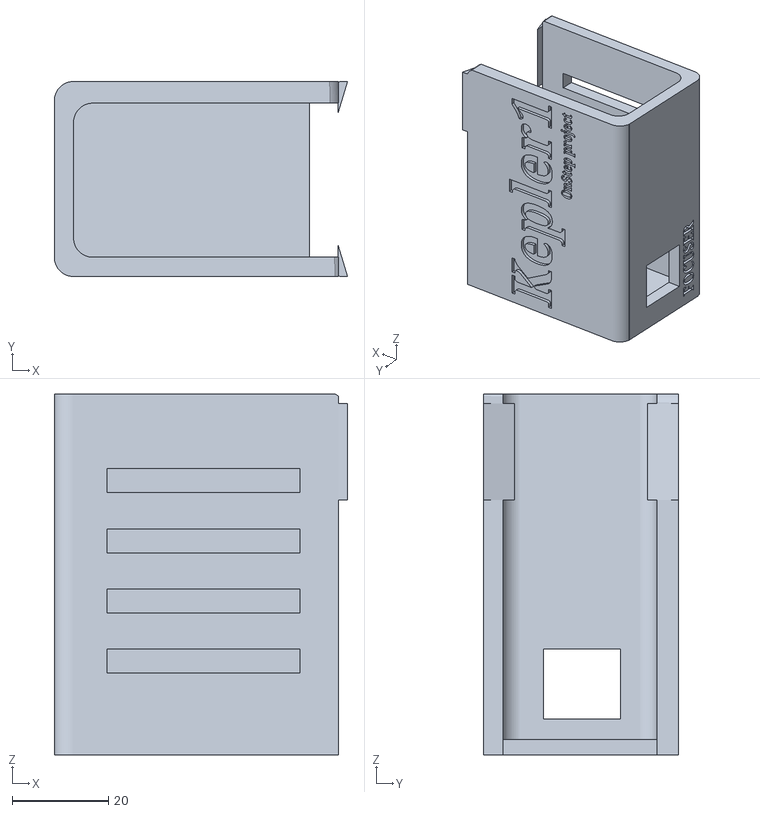
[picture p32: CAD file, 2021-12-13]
Hardware/FOCUSER-mechanism/FOC-motor/FOCUSER-V1-BOX.stl
60.9 x 40.6 x 75.0

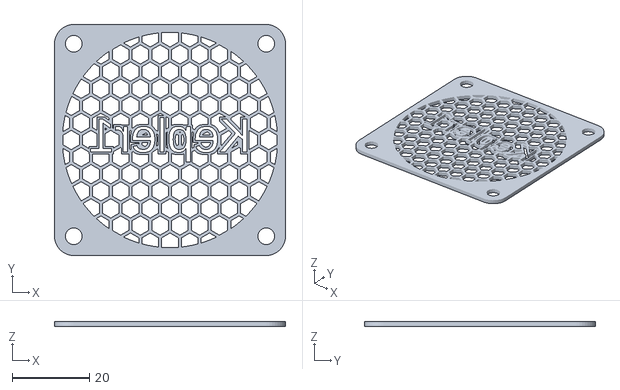
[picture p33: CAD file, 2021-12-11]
Hardware/BOX/customizable_fan_cover_V2_9.stl
60.0 x 60.0 x 1.30

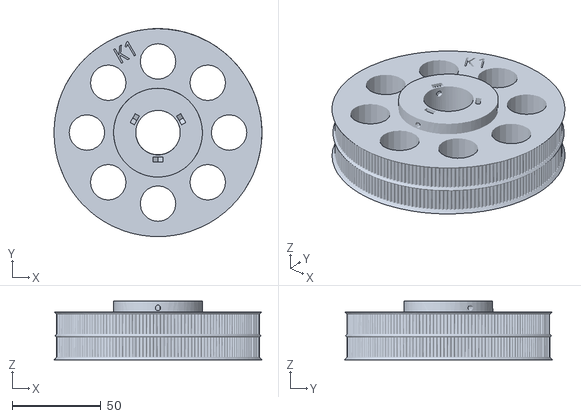
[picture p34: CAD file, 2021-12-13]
Hardware/DEC-mechanism/DEC-Puleggia/GT2_180-10mm_foro25_Doppia.stl
117.1 x 117.0 x 33.0

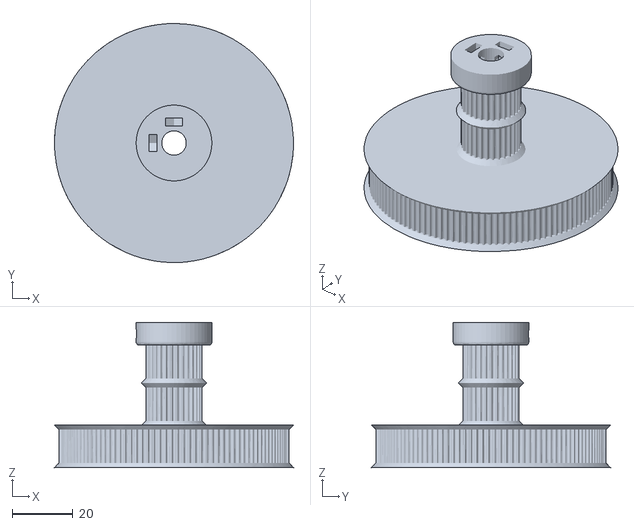
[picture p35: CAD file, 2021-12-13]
Hardware/DEC-mechanism/DEC-Puleggia/GT2-120tx30t_foro8_10mm.stl
78.8 x 78.9 x 47.8

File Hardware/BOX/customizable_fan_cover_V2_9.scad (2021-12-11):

/*
 * Customizable Fan Cover - https://www.thingiverse.com/thing:4837562
 * remixed by OutwardB - https://www.thingiverse.com/outwardb/about
 * original by Dennis Hofmann - https://www.thingiverse.com/mightynozzle/about
 * created 2018-02-22/2021-04-20
 * updated 2021-05-04
 * version v2.8.9
 *
 * Changelog
 * --------------
 * V2.9
 *      - Added 'centre_item_enabled' value for patterns (replaces text_replace_centre value)
 *      - Added Patterns
 *          --Half-Rings
 *          --CrossHex
 *          --CrossTri
 *          --Cross-Rings
 *          --Cross-Circles
 *
 * V2.8.9
 *      - Added Rounded Brick pattern
 *      - Fixes for multi-color export
 *
 * V2.8.8
 *      - Mutli-Color export options. If using a flat grill, easily add extra height to the text or SVG objects for change-at-layer-height multi-color printing
 *      - Small fix for camera options if using OpenSCAD to customize
 *      - Updated Brick pattern to give more control whilst using number_of_support_lines
 * 
 * V2.8.7
 *      - Added brick wall pattern
 *
 * V2.8.6
 *      - Text/SVG no longer rotates for flat frame type
 *
 * V2.8.5
 *      - Split up custom height and custom fan size settings so height can easily be changed whilst using preset values
 *      - More options for exporting SVG/text to print multi-color
 *
 * V2.8.4
 *      - Script now works in Thingiverse customizer. Added some stuff to make customization easier
 *      - Even more fixes and optimization
 *
 * V2.8.3
 *      - More multi-color testing
 *      - Fixed SVG import - I broke it in the last update :(
 *
 * V2.8.2
 *      - More script fixes and optimization
 *      - Re-worked preset values
 *
 * V2.8.1
 *      - Added Screw Count option. Can now select 2 or 4 holes/tabs
 *
 * V2.8
 *      - Re-arranged a load of values/settings to make customization easier (hopefully?)
 *      - Re-worked circular frame so that the screw mount now respect the min-border value! Looks much better for larger frame sizes IMO.
 *      - Fixed an issue with the domed grill so the grill should now be level with the outer cover
 *      - Reduced frame space now uses preset cover heights rather than a static value
 *      - Started playing with multi-colored text options. You can now export text on it's own
 *
 * V2.7.4
 *      - Re-worked 'none' pattern so SVGs/Text can now be used without a pattern
 *
 * V2.7.3
 *      - New frame option - reduced frame space
 *
 * V2.7.2
 *      - SVG Import is done
 *
 * V2.7.1
 *      - More text options, you can now have multiple lines of text
 *      - Frame space value (for flat grill)
 *
 * V2.7
 *      - Massive text overhaul
 *      - Outlined text is now much faster  to render
 *      - Dome twist option now works with text
 *      - More script optimization
 *
 * V2.6.7
 *      - Text transform tools. Move and rotate text
 *
 * V2.6.6
 *      - Added patterns - bahtinov01, windmill
 *      - Line Pattern now uses Number Of Support Lines value
 *      - Re-worked Square patern
 *      - Optimized a few patterns
 *      - Fixed an issue with the dot pattern
 *
 * V2.6.5
 *      - Fixed an small issue with text when using projection/dome settings
 *
 * V2.6.4
 *      - Spiral2 pattern, fixed a small issue with circular frame
 *
 * V2.6.3:
 *      - Carey pattern
 *      - Fixed cross pattern (now 45 deg and 0 support lines is an option)
 *
 * V2.6.2:
 *      - Cross pattern
 *
 * V2.6.1:
 *      - Bahtinov Pattern
 *      - More optimization and fixes
 *
 * V2.6:
 *      - SVG Import Preview
 *      - Added blank pattern good for logo cut outs
 *      - Preview now rotates if text is on the bottom
 *      - More Optimization & a bug fix (Fixed small gap in domed grills)
 *      - Started to properly label script - anyone wanting to learn from this should now have a much easier time of it
 *
 * V2.5.3:
 *      - More text options! Set text_thickness to 0 for a block item (useful for logos).
 * 
 * V2.5.2:
 *      - Bio-Hazard Pattern
 *      - More optimization and bug fixes
 * 
 * V2.5.1:
 *      - Re-arranged some values to make customization easier
 *      - Optimization and bug fixes
 *
 * V2.5:
 *      - Added a protector feature for circular & full frame types (W.I.P)
 *
 * V2.4.6:
 *      - Added Spiral Pattern. 
 *
 * V2.4.5:
 *      - Added Atom Pattern. 
 *
 * V2.4.4:
 *      - Added Tear Drop Pattern. 
 *      - Teardrop & aperture patterns have an option to remove the centre item if using text
 *
 * V2.4.3:
 *      - Added custom cover height presets for domed options
 *
 * V2.4.2:
 *      - Updated text - it now is generated upside down when using a flat grill
 *
 * V2.4.1:
 *      - Fized patterns - fancy, fancy1, fancy2
 *
 * V2.4:
 *      - Added patterns - web, fancy, fancy1, fancy2 based on upload by Sislar (https://www.thingiverse.com/sislar/about)
 *
 * V2.3:
 *      - Merged projection by agnoia (https://www.thingiverse.com/agnoia/about)
 * 
 * V2.2:
 *      - Merged text generator by elopus001 (https://www.thingiverse.com/elopus001/about)
 * 
 * V2.1:
 *      - Merged patterns - random, zigzag & none by agnoia (https://www.thingiverse.com/agnoia/about)
 *      - Added patterns - trihole, pentagon
 * 
 * V2:
 *      - Added circular style frame option
 * --------------
 *
 * This work is licensed under the Creative Commons - Attribution - Non-Commercial - ShareAlike license.
 * https://creativecommons.org/licenses/by-nc-sa/3.0/
 */


 // Parameter Section //
//-------------------//

/* [General] */
// How are you customizing this thing? This will set the default font and camera options
What_app_are_you_using = "Thingiverse Customizer"; //[Thingiverse Customizer,OpenSCAD]


/* [Frame] */
// Choose between presets of known and common fan sizes
fan_preset = "60"; //[25:25mm,30:30mm,40:40mm,50:50mm,60:60mm,70:70mm,80:80mm,92:92mm,120:120mm,140:140mm]

// Select a frame style
frame_option = "full"; //[full,reduced,circular]

// Select a frame type (Reduced frame style will not work with the Domed options!)
frame_type = "reduced"; //[flat,bladeSpace,reducedSpace,domedFull,domed,domedTwist]

// How many Screw Tabs/Holes
screw_count = 4; //[2,4]

// If you need countersunk holes, you can activate it here
screw_hole_chamfer = "no"; //[no,top,bottom,top_and_bottom]

// Minimum Outer Border Size. I recommend to use two/four/six... times of your line width setting of your slicer. Simplify3D uses 0.48mm line width by default if you are using a 0.4mm nozzle. Cura uses 0.4mm line width
min_border_size_in_millimeter = 2; //[0.1:0.1:15]


/* [Pattern] */
// Choose between a grill pattern
grill_pattern = "honeycomb"; //[aperture,atom,bahtinov,bahtinov01,bio,brick,brick-rounded,carey,cross,crosshair,crosshex,crosstri,cross-rings,dot,fancy,fancy1,fancy2,grid,half-rings,honeycomb,line,pentagon,random,spiral,square,teardrop,triangle,trihole,web,windmill,zigzag,blank,none,svg]

// Only for some patterns, spiral, teardrop, crossheirs/hex/tri patterns - no will remove the centre item
centre_item_enabled = "no"; //[yes,no]

// Set the angle of the pattern around the center of the cover
grill_pattern_rotation = 0; //[0:5:360]

// Size of the pattern lines. I recommend to use two/four/six... times of your line width setting of your slicer. Simplify3D uses 0.48mm line width by default if you are using a 0.4mm nozzle. Cura uses 0.4mm line width.
line_size_in_millimter = 0.8; //[0.3:0.02:4]

// Space between two lines of your pattern. If you choose aperture pattern, this value set the size of the center octagon.
line_space_in_millimeter = 5; //[1:0.1:50]

// number of straight lines supporting some patterns (e.g. spiral, crosshair, square, etc ).
number_of_support_lines = 6;  //[0:1:36]


/* [Text] */
// Text to add into the grill. Pro-Tip: You can use logo-fonts to add a logo!
grill_text = "Kepler1";

// Second line - leave empty if un-needed
grill_text_02 = "";

// Font for the grill text. (Be careful not to create an un-printable file!)
grill_text_font = "";

// Font size of the grill text.
grill_text_size = 9; //[0.5:0.5:100]

// Thickness of text outline, set to 0 for a block item, 1 or more for an outline
text_thickness = 0.5; //[0:0.1:10]

/* [Text - Advanced Settings] */

// Move text left/right
grill_text_x_nudge = 0;

// Move text up/down
grill_text_y_nudge = 0;

// Rotate text (Inverted if using a flat grill)
grill_text_rotate = 0; //[-180:0.1:180]

// Extra space between text line 1 & 2
grill_text_space = 1; //[0:0.1:50]


/* [Import SVG] */
// Set to yes to enable (Must be using OpenSCAD, will not work in Thingiverse customizer!)
svg_import_enabled = "no"; //[yes,no]

// Select the file to import (must be a SVG | set pattern type to svg to use as a cut out. E.G. C:\TempFolder\File.SVG)
file_to_import = "";

// Scale the SVG
file_scale = 0.2; //[0.001:0.001:50]

// Thickness of SVG outline, set to 0 for a block item, 1 or more for an outline
svg_thickness = 0; //[0:0.1:10]

// Move SVG left/right
svg_x_nudge = 0;
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

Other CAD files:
Hardware/DEC-mechanism/DEC-Puleggia/DEC_GT2_30T_10mm_doppia.scad
Hardware/DEC-mechanism/DEC-Puleggia/Pulley_T-MXL-XL-HTD-GT2_N-tooth.scad

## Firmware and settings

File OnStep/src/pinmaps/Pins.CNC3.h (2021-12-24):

// -------------------------------------------------------------------------------------------------
// Pin map for CNC Shield Version 3 (with WeMos D1 R32)

// Note: SPI for TMC drivers: GPIO32 (MOSI), GPIO33 (SCK), GPIO15 (CS Axis1) on WeMos D1 R32 PCB are more difficult to wire into but optional. GPIO18 (CS Axis2) is on top.

#if defined(ESP32)

// Serial2 (SerialB) needs to be re-mapped to GPIO13 (RX) and GPIO5 (TX)
#define SERIAL_B_RX          13
#define SERIAL_B_TX           5

// The multi-purpose pins (Aux3..Aux8 can be analog pwm/dac if supported)
#define Aux2                 33     // ESP8266 RST control, or Axis2 CS support - 18 OK
#define Aux3                 21     // Home SW for Axis1, or I2C SDA {assuming default SCL/SDA pins are present}
#define Aux4                 22     // Home SW for Axis2, or I2C SCL
#define Aux7                 39     // Limit SW, PPS, etc.
#define Aux8                 15     // OneWire, Status LED, Status2 LED, Reticle LED, etc. - 23 OK

// Misc. pins
#ifndef OneWirePin
  #define OneWirePin       Aux8     // Default Pin for OneWire bus
#endif
#define AddonBootModePin     27     // ESP8266 GPIO0 (Dir2)
#define AddonResetPin      Aux2     // ESP8266 RST

// The PEC index sense is a logic level input, resets the PEC index on rising edge then waits for 60 seconds before allowing another reset
#define PecPin               36     // [input only 36]
#define AnalogPecPin         A0     // PEC Sense, analog or digital (GPIO36)

// The status LED is a two wire jumper with a 10k resistor in series to limit the current to the LED
#define LEDnegPin          Aux8     // Drain
#define LEDneg2Pin         Aux8     // Drain
#define ReticlePin         Aux8     // Drain

// For a piezo buzzer
#define TonePin               32     // Tone - 2 OK

// The PPS pin is a 3.3V logic input, OnStep measures time between rising edges and adjusts the internal sidereal clock frequency
#define PpsPin             Aux7     // PPS time source, GPS for example

#define LimitPin           Aux7     // The limit switch sense is a logic level input normally pull high (2k resistor,) shorted to ground it stops gotos/tracking

// Axis1 RA/Azm step/dir driver
#define Axis1_EN             12     // Enable [must be low at boot 12]
#define Axis1_M0             19     // Microstep Mode 0 or SPI MOSI - 32 OK
#define Axis1_M1             18     // Microstep Mode 1 or SPI SCK - 33 OK
#define Axis1_M2             0     // Microstep Mode 2 or SPI CS - 15 OK
#define Axis1_M3           Aux2     // SPI MISO/Fault
#define Axis1_STEP           26     // Step
#define Axis1_DIR            16     // Dir
#define Axis1_DECAY    Axis1_M2     // Decay mode
#define Axis1_HOME         Aux3     // Sense home position

// Axis2 Dec/Alt step/dir driver
#define Axis2_EN         SHARED     // Enable pin control shared with Axis1
#define Axis2_M0             2      // Microstep Mode 0 or SPI MOSI - 32 OK
#define Axis2_M1             4      // Microstep Mode 1 or SPI SCK - 33 OK
#define Axis2_M2             23     // Microstep Mode 2 or SPI CS - 0 OK
#define Axis2_M3           Aux2     // SPI MISO/Fault
#define Axis2_STEP           25     // Step
#define Axis2_DIR            27     // Dir
#define Axis2_DECAY    Axis2_M2     // Decay mode
#define Axis2_HOME         Aux4     // Sense home position

// For rotator stepper driver
#define Axis3_EN         SHARED     // Enable pin control shared with Axis1
#define Axis3_STEP           32     // Step - 19 OK
#define Axis3_DIR            14     // Dir

// For focuser1 stepper driver
#define Axis4_EN         SHARED     // Enable pin control shared with Axis1
#define Axis4_STEP           17     // Step
#define Axis4_DIR            14     // Dir

// For focuser2 stepper driver
#define Axis5_EN         SHARED     // Enable pin control shared with Axis1
#define Axis5_STEP           32     // Step - 19 OK
#define Axis5_DIR            14     // Dir

// ST4 interface
#define ST4RAw               34     // ST4 RA- West [input only 34]
#define ST4DEs               33     // ST4 DE- South - 18 OK
#define ST4DEn               33     // ST4 DE+ North - 4 OK
#define ST4RAe               35     // ST4 RA+ East [input only 35]

#else
#error "Wrong processor for this configuration!"

#endif

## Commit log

2021-10-27 Added stepperMotorCtrl.ino
2021-10-28 Added accelerationon stepper motors
2021-10-30 Added Esp32 project
2021-11-03 Added two stepper motors sketch
2021-11-03 Deleted the elementary sketch for stepper motor
2021-12-11 Commit before the pull request after long time
    [DEC_GT2_30T_10mm_doppia.scad, DEC_GT2_30T_10mm_doppia_1.stl, Pulley_T-MXL-XL-HTD-GT2_N-tooth.scad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]
2021-12-13 Untrack files in .gitignore
    [guide-11.csv]
2021-12-13 Change title "Motorize a 1980 telescope"
2021-12-13 Hardware STL files
    [DEC_GT2_30T_10mm_doppia_1.stl, FOCUSER-V1-BOX.stl, FOCUSER-V1.stl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]
2021-12-16 Added analysis
    [guide-11.csv]
2021-12-16 Added OnStep pinmaps and Config.h, bearing image
2021-12-16 Try to commit with * in .gitignore
    [DEC_GT2_30T_10mm_doppia.scad, FOCUSER-V1-BOX.stl, FOCUSER-V1.stl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]
2021-12-16 Documentation cut to the essential
2021-12-21 Add Hardware and updated .gitignore
    [BOX-V3-TOP.stl, BOX-V3.stl, DEC-V3+-box.stl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]
2021-12-24 Added DEC V1+ test and updated pinmanp
    [guide-7.csv]
2021-12-24 Added circuit design
    [circuit-design.fzz]
2021-12-24 Prepare to publish
    [circuit-design.fzz]
2021-12-24 Untrack files in .gitingore for publishing
    [circuit-design.fzz, guide-11.csv, guide-7.csv]
2021-12-24 Share last informations
    [circuit-design.fzz, guide-11.csv, guide-7.csv]
